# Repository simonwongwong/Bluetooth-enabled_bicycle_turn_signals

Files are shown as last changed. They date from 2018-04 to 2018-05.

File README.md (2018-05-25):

# Bluetooth-enabled bicycle turn signal
A turn signal for bikes!

**Motivation**

After commuting to work every day on my bicycle, I decided that I needed a better way to signal my turns. Sticking my arms out can be dangerous, especially if you're riding downhill in the rain (as is common in Vancouver).

I had recently got an Arduino and wanted to embark on my first project, so I decided to kill two birds with one stone!

I wanted something waterproof that I can use in the rain, and something detachable so it wouldn't get stolen, it needed to be detachable/wireless.

The plan was to have a couple of switches embedded into the handlebars (for power and for turn signal), use a Bluetooth transmitter (HC-05) for communication, and have an Arduino Nano to control it all with an 18650 lithium-ion battery (controlled with a 134N3P chip) for power. On the other end of the bike, there are two 8x8 LED matrices controlled by MAX7219 controllers, a Bluetooth receiver (HC-05), an ATMEGA328P chip to control all the components and an 18650 (or 14500) lithium-ion battery for power. I also added a Qi wireless charging receiver to charge the battery without opening the lights enclosure.

**Action shots**

Here's a gif of it in action:

it's working!

A closeup of the updated slim case with all the gubbins:
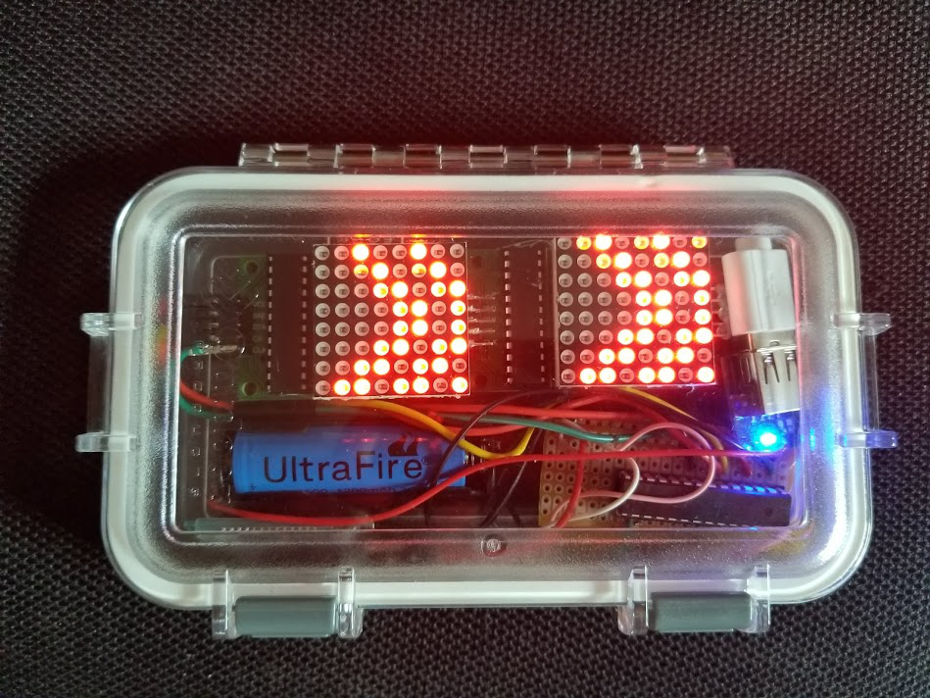
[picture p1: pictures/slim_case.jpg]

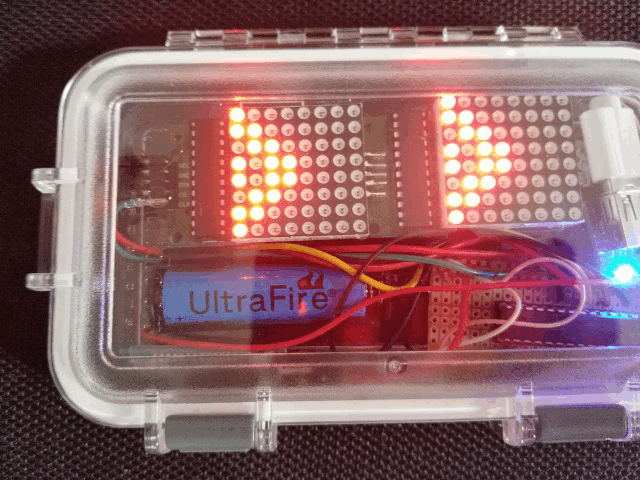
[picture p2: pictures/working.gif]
moving


If you don't like my boring arrows, make any indicator animation you want using my 8x8 LED byte generator found on my [LED_byte_matrix_generator repo](https://github.com/simonwongwong/LED_byte_matrix_generator)

Full parts and tools requirements can be found on the [hackster.io page](hackster.io/simonwongwong/bluetooth-enabled-bicycle-turn-signal-2f4f5d)

# Wiring diagrams

Diagram for handlebar/controller:

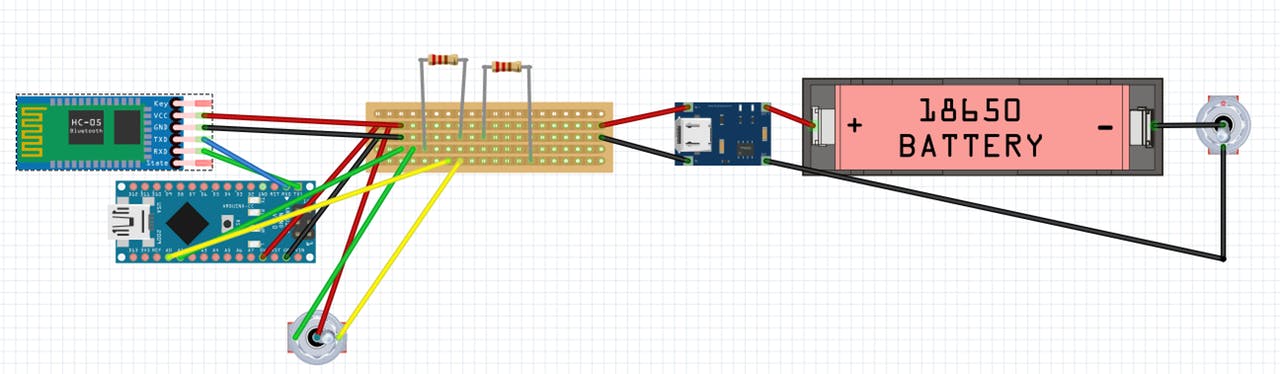
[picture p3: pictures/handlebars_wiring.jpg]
Inside the handlebars


Diagram for lights enclosure:

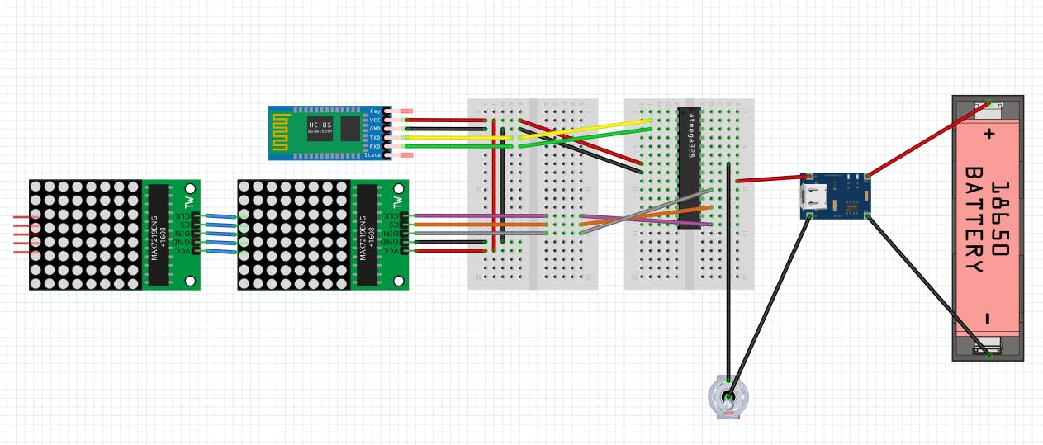
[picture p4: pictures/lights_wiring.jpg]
lights wiring


# Setup instructions:

* Set up the HC-05 Bluetooth modules to pair with each other using a master-slave setup [(instructions)](https://howtomechatronics.com/tutorials/arduino/how-to-configure-pair-two-hc-05-bluetooth-module-master-slave-commands/)
  - Other Bluetooth modules with similar functionality can be used
* Upload code for the [lights](code_for_lights.ino) and the [handlebars](code_for_handlebars_controller.ino) to the Arduino Nano (or any other ATMEGA328P based chip) 
* Wire everything up according to the wiring diagrams
  - if using a reed switch to control power to the lights, you'll need a magnet

# Variation/upgrade ideas

* **Reed switch to control power to the lights**. If your case is too slim for a toggle switch (like my latest iteration) or you're worried about the waterproof-ness of the case, a reed switch could be used.
  - New wiring diagram:
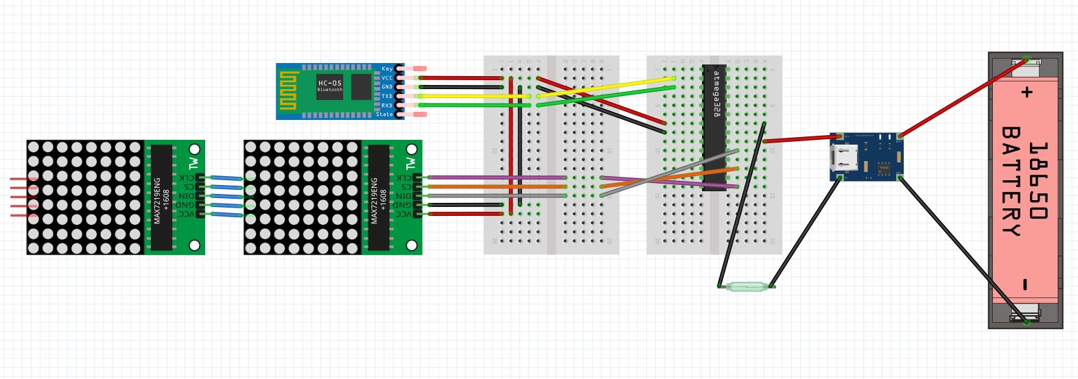
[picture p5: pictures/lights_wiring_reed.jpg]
with reed switch
   
  - A magnet attached to the light mount can turn the lights on and the lights can be turned off by taking the lights off the mount
  - Or a second magnet can be used to change the flux path and open the reed switch like so:
   flux change
* **Neopixel rings and jewels as a turn signal**, like a car with the outer ring in red and the inner jewel lit up amber and flashing when turning

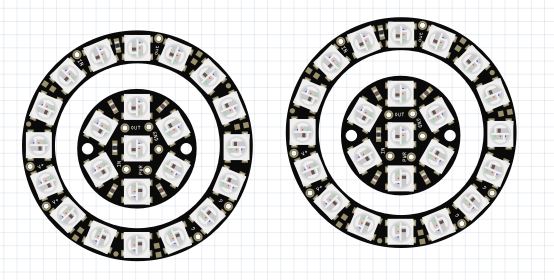
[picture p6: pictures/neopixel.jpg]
neopixel idea
   
* **Add an accelerometer** to detect slowing down and display a slowing down animation or flash amber lights

* **Use large/bright LED strips on the seatstays instead of LED matrix for better visibility** Because the LED matrix is hard to see, especially in the daylight, a better/more obvious variant of this project can be built with bright LED strips attached to the seatstays of the bike. While this will improve visibility, it won't be as removable. Another similar idea is to use bright LED strips protruding as rods (horizontally, left and right) and blink them like [this](https://i.imgur.com/lOJ0493.jpg).

# Pictures of the build

Internals:

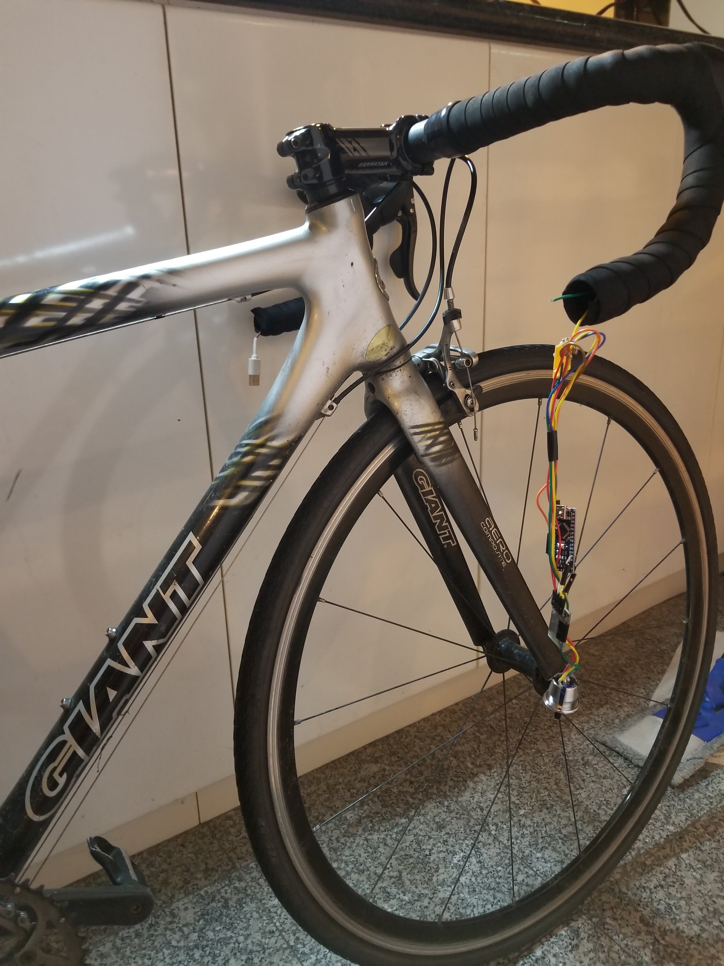
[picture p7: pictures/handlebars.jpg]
Internals of handlebars


Note: Bluetooth module, Arduino Nano and PCB separated from battery by a long ~1m cable

Image of handlebar batteries:

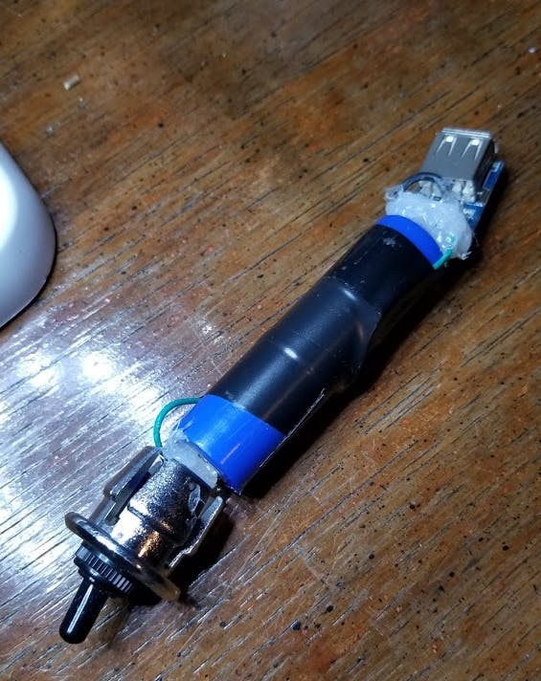
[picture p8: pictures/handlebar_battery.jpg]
handlebar batteries


Testing lights before gluing everything and closing the case:

testing

Mounted on my bike:

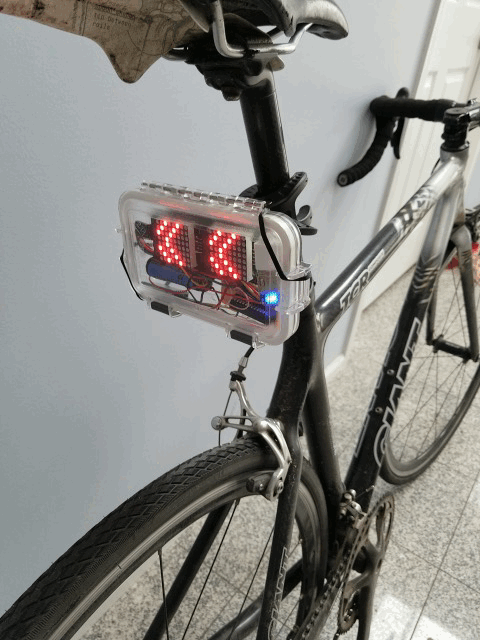
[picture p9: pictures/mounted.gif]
mounted


Message me for more details if you want to make one for yourself

Thanks for reading!

(OLD PICTURES BELOW)

Lights enclosure with breadboards wired up:

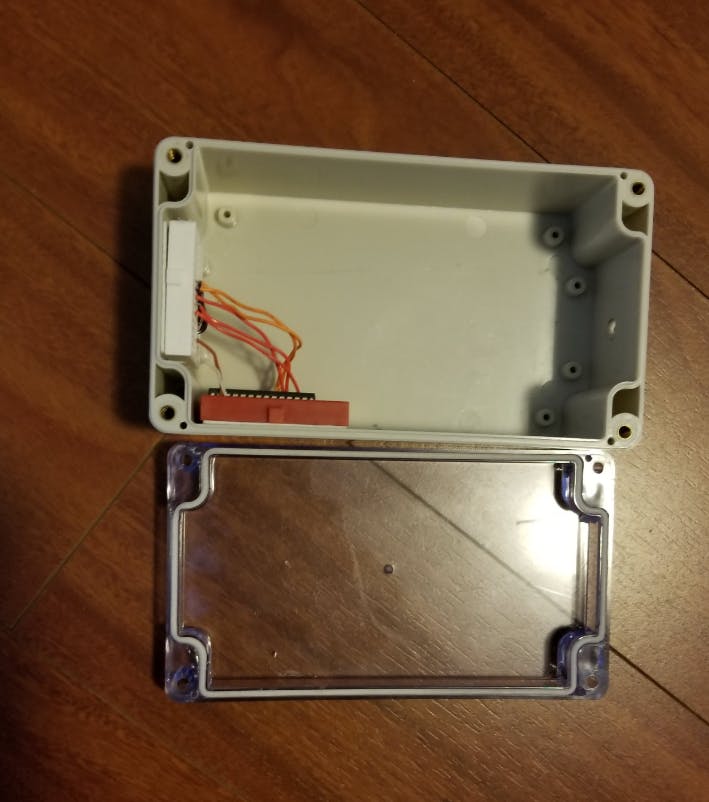
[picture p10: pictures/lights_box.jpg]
lights_box


Qi wireless charger attached to battery pack:

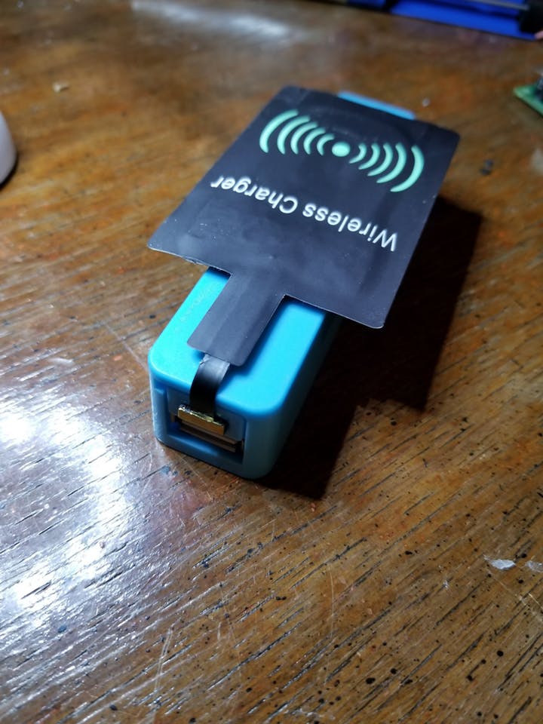
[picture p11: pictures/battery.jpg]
battery


Fully assembled:

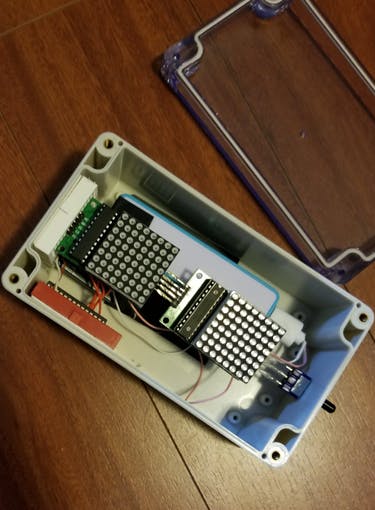
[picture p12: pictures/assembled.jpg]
assembled


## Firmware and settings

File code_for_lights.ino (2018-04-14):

#include "LedControl.h"

LedControl lc = LedControl(13, 9, 11, 2); //DIN, CLK, CS
int dlay = 50; // delay of 50ms per frame
char state = 'I'; //initial state (idle)

//left turn animation
const byte LEFT[][8] = {
  {
    B00000000,
    B00000000,
    B00000000,
    B00000001,
    B00000001,
    B00000000,
    B00000000,
    B00000000
  }, {
    B00000000,
    B00000000,
    B00000001,
    B00000010,
    B00000010,
    B00000001,
    B00000000,
    B00000000
  }, {
    B00000000,
    B00000001,
    B00000010,
    B00000100,
    B00000100,
    B00000010,
    B00000001,
    B00000000
  }, {
    B00000001,
    B00000010,
    B00000100,
    B00001001,
    B00001001,
    B00000100,
    B00000010,
    B00000001
  }, {
    B00000010,
    B00000100,
    B00001001,
    B00010010,
    B00010010,
    B00001001,
    B00000100,
    B00000010
  }, {
    B00000100,
    B00001001,
    B00010010,
    B00100100,
    B00100100,
    B00010010,
    B00001001,
    B00000100
  }, {
    B00001001,
    B00010010,
    B00100100,
    B01001001,
    B01001001,
    B00100100,
    B00010010,
    B00001001
  }, {
    B00010010,
    B00100100,
    B01001001,
    B10010010,
    B10010010,
    B01001001,
    B00100100,
    B00010010
  }, {
    B00100100,
    B01001001,
    B10010010,
    B00100100,
    B00100100,
    B10010010,
    B01001001,
    B00100100
  }, {
    B01001001,
    B10010010,
    B00100100,
    B01001000,
    B01001000,
    B00100100,
    B10010010,
    B01001001
  }, {
    B10010010,
    B00100100,
    B01001000,
    B10010000,
    B10010000,
    B01001000,
    B00100100,
    B10010010
  }, {
    B00100100,
    B01001000,
    B10010000,
    B00100000,
    B00100000,
    B10010000,
    B01001000,
    B00100100
  }, {
    B01001000,
    B10010000,
    B00100000,
    B01000000,
    B01000000,
    B00100000,
    B10010000,
    B01001000
  }, {
    B10010000,
    B00100000,
    B01000000,
    B10000000,
    B10000000,
    B01000000,
    B00100000,
    B10010000
  }, {
    B00100000,
    B01000000,
    B10000000,
    B00000000,
    B00000000,
    B10000000,
    B01000000,
    B00100000
  }, {
    B01000000,
    B10000000,
    B00000000,
    B00000000,
    B00000000,
    B00000000,
    B10000000,
    B01000000
  }, {
    B10000000,
    B00000000,
    B00000000,
    B00000000,
    B00000000,
    B00000000,
    B00000000,
    B10000000
  }
};
//right turn animation
const byte RIGHT[][8] = {
  {
    B00000000,
    B00000000,
    B00000000,
    B10000000,
    B10000000,
    B00000000,
    B00000000,
    B00000000
  }, {
    B00000000,
    B00000000,
    B10000000,
    B01000000,
    B01000000,
    B10000000,
    B00000000,
    B00000000
  }, {
    B00000000,
    B10000000,
    B01000000,
    B00100000,
    B00100000,
    B01000000,
    B10000000,
    B00000000
  }, {
    B10000000,
    B01000000,
    B00100000,
    B10010000,
    B10010000,
    B00100000,
    B01000000,
    B10000000
  }, {
    B01000000,
    B00100000,
    B10010000,
    B01001000,
    B01001000,
    B10010000,
    B00100000,
    B01000000
  }, {
    B00100000,
    B10010000,
    B01001000,
    B00100100,
    B00100100,
    B01001000,
    B10010000,
    B00100000
  }, {
    B10010000,
    B01001000,
    B00100100,
    B10010010,
    B10010010,
    B00100100,
    B01001000,
    B10010000
  }, {
    B01001000,
    B00100100,
    B10010010,
    B01001001,
    B01001001,
    B10010010,
    B00100100,
    B01001000
  }, {
    B00100100,
    B10010010,
    B01001001,
    B00100100,
    B00100100,
    B01001001,
    B10010010,
    B00100100
  }, {
    B10010010,
    B01001001,
    B00100100,
    B00010010,
    B00010010,
    B00100100,
    B01001001,
    B10010010
  }, {
    B01001001,
    B00100100,
    B00010010,
    B00001001,
    B00001001,
    B00010010,
    B00100100,
    B01001001
  }, {
    B00100100,
    B00010010,
    B00001001,
    B00000100,
    B00000100,
    B00001001,
    B00010010,
    B00100100
  }, {
    B00010010,
    B00001001,
    B00000100,
    B00000010,
    B00000010,
    B00000100,
    B00001001,
    B00010010
  }, {
    B00001001,
    B00000100,
    B00000010,
    B00000001,
    B00000001,
    B00000010,
    B00000100,
    B00001001
  }, {
    B00000100,
    B00000010,
    B00000001,
    B00000000,
    B00000000,
    B00000001,
    B00000010,
    B00000100
  }, {
    B00000010,
    B00000001,
    B00000000,
    B00000000,
    B00000000,
    B00000000,
    B00000001,
    B00000010
  }, {
    B00000001,
    B00000000,
    B00000000,
    B00000000,
    B00000000,
    B00000000,
    B00000000,
    B00000001
  }
};
//idle animation (forward)
const byte IDLE[][8] = {
  {
    B00000000,
    B00000000,
    B00000000,
    B00000000,
    B00000000,
    B00000000,
    B00000000,
    B00011000
  }, {
    B00000000,
    B00000000,
    B00000000,
    B00000000,
    B00000000,
    B00000000,
    B00011000,
    B00000000
  }, {
    B00000000,
    B00000000,
    B00000000,
    B00000000,
    B00000000,
    B00011000,
    B00000000,
    B00111100
  }, {
    B00000000,
    B00000000,
    B00000000,
    B00000000,
    B00011000,
    B00000000,
    B00111100,
    B00000000
  }, {
    B00000000,
    B00000000,
    B00000000,
    B00011000,
    B00000000,
    B00111100,
    B00000000,
    B01111110
  }, {
    B00000000,
    B00000000,
    B00011000,
    B00000000,
    B00111100,
    B00000000,
    B01111110,
    B00000000
  }, {
    B00000000,
    B00011000,
    B00000000,
    B00111100,
    B00000000,
    B01111110,
    B00000000,
    B11111111
  }, {
    B00011000,
    B00000000,
    B00111100,
    B00000000,
    B01111110,
    B00000000,
    B11111111,
    B00000000
  }, {
    B00000000,
    B00111100,
    B00000000,
    B01111110,
    B00000000,
    B11111111,
    B00000000,
    B00000000
  }, {
    B00111100,
    B00000000,
    B01111110,
    B00000000,
    B11111111,
    B00000000,
    B00000000,
    B00000000
  }, {
    B00000000,
    B01111110,
    B00000000,
    B11111111,
    B00000000,
    B00000000,
    B00000000,
    B00000000
  }, {
    B01111110,
    B00000000,
    B11111111,
    B00000000,
    B00000000,
    B00000000,
    B00000000,
    B00000000
  }, {
    B00000000,
    B11111111,
    B00000000,
    B00000000,
    B00000000,
    B00000000,
    B00000000,
    B00000000
  }, {
    B11111111,
    B00000000,
    B00000000,
    B00000000,
    B00000000,
    B00000000,
    B00000000,
    B00000000
  }
};
void setup() {
  Serial.begin(38400);
  lc.shutdown(0, false); // Wake up displays
  lc.shutdown(1, false);
  lc.setIntensity(0, 15); // Set intensity levels
  lc.setIntensity(1, 15);
  lc.clearDisplay(0);  // Clear Displays
  lc.clearDisplay(1);
}
//read value from handlebars
void read() {
  while (Serial.available() > 0) { //flush useless data in stream
    char value = Serial.read();
    if (value == 'R' || value == 'L' || value == 'I') {
      state = value;
    }
  }
}

}
void loop() {
  int i = 0;
  int len;
  Serial.begin(38400);
  do {
    if (state == 'R') {
      len = sizeof(RIGHT) / 8;
      for (int j = 0; j < 8; j++) {
        lc.setRow(0, j, RIGHT[i][j]);
        lc.setRow(1, j, RIGHT[i][j]);
      }
    }
    if (state == 'L') {
      len = sizeof(LEFT) / 8;
      for (int j = 0; j < 8; j++) {
        lc.setRow(0, j, LEFT[i][j]);
        lc.setRow(1, j, LEFT[i][j]);
      }
    }
    if (state == 'I') {
      len = sizeof(IDLE) / 8;
      for (int j = 0; j < 8; j++) {
        lc.setRow(0, j, IDLE[i][j]);
        lc.setRow(1, j, IDLE[i][j]);
      }
    } 
    if (i < len - 1) {
      i++;
    } else {
      i = 0;
    }
    delay(dlay);
  } while (Serial.available() < 1);
  read();
}

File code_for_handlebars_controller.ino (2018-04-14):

const int yellow = A0; //colour of wire connected to analog input (LEFT turn)
const int green = A1; //colour of wire connected to analog input (RIGHT turn)
int greenval; //analog reading for green wire (A1)
int yellowval;//analog reading for yellow wire (A1)

char current = 'I'; 
char switcher = 'I'; //default IDLE animation

void setup() {
Serial.begin(38400);

}

void loop() {
  //read switch 
  greenval = analogRead(green);
  yellowval = analogRead(yellow);
  if (greenval > 500) {
    switcher = 'R';
  } else if (yellowval > 500) {
    switcher = 'L';
  } else {
    switcher = 'I';
  }
  //only transmit a signal if it has changed (saves power)
  if (current != switcher) {
    current = switcher;
    Serial.println(switcher);
  }
  delay(500);
}

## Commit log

2018-04-14 added code and wiring diagrams
    [handlebars.fzz, lights.fzz]
2018-04-16 Updated photos with new enclosure
2018-04-18 reed switch version
